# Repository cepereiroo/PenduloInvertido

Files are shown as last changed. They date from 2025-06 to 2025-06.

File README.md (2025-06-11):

# PenduloInvertido_Cecilia
En este repositorio se encuentra tanto la práctica 4 cómo la práctica 6 de la asignatura de Teoría de Control.

Además en la carpeta DiseñoPendulo se encuentra el esquemático eléctrico, el diseño de la PCB y el modelo 3D STL del chasis para su impresión.

**PRÁCTICA 4 - PID en tiempo discreto** 

Esta práctica tiene como objetivo implementar una biblioteca de controladores PID en tiempo discreto para ser utilizada en un microcontrolador ESP32, con aplicación directa en el control de un péndulo invertido. Esta biblioteca será utilizada en el desarrollo del proyecto de control descrito en el capítulo 6 del guión de prácticas. 

Se desarrollarán tres variantes del controlador PID en tiempo discreto: 

- **PID** : utiliza aproximaciones hacia atrás para las derivadas y sumas acumulativas para la integral. 
- **PID como filtro IIR**: modelado mediante transformada Z, facilitando su implementación como filtro digital. 
- **PID filtro baja** : se le pone un filtro al término derivativo para evitar que el ruido o los cambios bruscos del error afecten al control. 

Cada implementación está basada en los pseudocódigos del guión.  

Esta práctica está encapsulada en la carpeta libraries donde nos encontraremos :  

**I2Cdev/** 

Contiene archivos fuente y cabeceras que permiten la comunicación mediante el protocolo I2C. Es una biblioteca comúnmente usada para facilitar la lectura y escritura con sensores como el MPU6050 

**MPU6050/** 

Incluye las definiciones y funciones específicas para el sensor MPU6050, que proporciona mediciones de aceleración y giroscopio. Esta biblioteca se apoya en I2Cdev para obtener los datos del sensor y es esencial para calcular la posición y velocidad angular del péndulo. 

**PIDController/** 

Es la biblioteca desarrollada para está práctica para implementar los tres tipos de controladores PID discretos: 

- PID directo 
- PID como filtro IIR 
- PID filtro pasa baja

Dentro de cada carpeta estarán los archivos .h y .cpp con la implementación de las clases PID 

Se añadirá además una carpeta examples que contendrá tres ejemplos simples que muestran cómo usar cada una de las variantes del controlador PID implementadas. 

**CodigoCompletoPendulo.ino** 

Este es el sketch código principal de Arduino que integra las bibliotecas anteriores. Aquí se encuentra el código de control que: 

- Lee el ángulo del péndulo usando el MPU6050 
- Calcula la señal de control con el PID 
- Aplica la corrección al actuador 
- Permite probar y comparar las distintas variantes del controlador PID 

**PRÁCTICA 6 - Péndulo Invertido** 

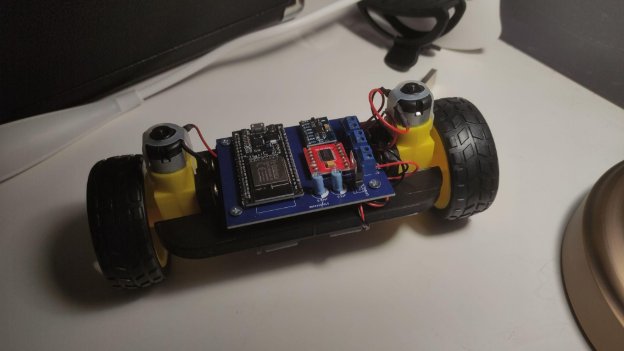
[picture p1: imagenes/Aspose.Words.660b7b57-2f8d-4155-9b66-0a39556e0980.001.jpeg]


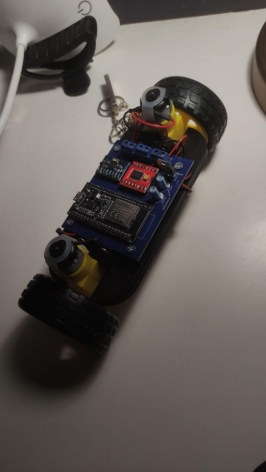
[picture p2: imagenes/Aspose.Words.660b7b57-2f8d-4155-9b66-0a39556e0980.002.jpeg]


En esta memoria se documenta el desarrollo de un prototipo funcional de un sistema de control para un péndulo invertido sobre ruedas, utilizando una ESP32 como unidad de control. El objetivo principal es mantener el equilibrio del péndulo en posición vertical mediante un controlador PID. 

Metodología seguida 

**Revisión de trabajos previos** 

Se investigaron diferentes proyectos relacionados con el péndulo invertido. 

**Definición de objetivos** 

Los objetivos del sistema se centraron en la estabilidad, la capacidad de recuperación tras perturbaciones y la interacción con el usuario mediante mando Bluetooth. 

**Selección del hardware** 

Se eligieron componentes accesibles y económicos que permitan un montaje sencillo y una buena integración con el entorno de desarrollo en C++. 

**Diseño del sistema físico** 

El chasis se diseñó buscando una estructura equilibrada, estable y lo más ligera posible, para facilitar la respuesta del sistema. 

**Programación y pruebas de control PID** 

Se implementó un controlador PID discreto en la ESP32, aplicando distintas versiones del algoritmo (con y sin filtro derivativo) y ajustando sus constantes. 
# **6.1 Hardware**   
**ESP32** 

Como unidad central de procesamiento utilicé una placa ESP32, concretamente un modelo disponible en Amazon por unos 11€. Este microcontrolador se conecta al ordenador mediante USB y permite cargar el código desde el entorno de Arduino.  

**MPU-6050** 

El sensor MPU-6050 fue el elegido para medir la orientación del robot, ya que incorpora un acelerómetro y un giroscopio en un solo módulo. Esta información es clave para mantener el equilibrio, especialmente con un margen inferior a 5 grados de inclinación.  

**Condensadores** 

En el circuito se añadieron dos condensadores: uno de 0,1 µF y otro de 0,22 µF. Estos se usaron para estabilizar la señal y reducir el ruido en ciertas conexiones críticas del sistema. 

**Bloques terminales** 

Para facilitar la conexión entre la batería y los motores, se instalaron bloques terminales. Esto permite una conexión firme y organizada del cableado. Se usaron tres en total, uno para cada motor y otro para la alimentación principal. 

**TB6612FNG** 

Para el control de los motores se optó por el TB6612FNG, un driver más eficiente y moderno que el clásico puente H. Con un precio inferior a los 2€, permite controlar dos motores de forma simultánea e independiente.  

**Batería** 

Alimenté el sistema con un portapilas de 4 pilas AA, conectado directamente a los bornes de alimentación de la placa. 

**Motores y ruedas** 

Se emplearon motores DC con reductora, muy comunes en robótica educativa. Vienen acompañados de ruedas compatibles que se acoplan directamente al eje del motor, facilitando el montaje. 

**Regulador de voltaje** 

Para asegurar un suministro eléctrico estable, se incorporó un regulador LM7805. Este componente mantiene la tensión en 5V, protegiendo así los elementos sensibles del circuito.  

# 6.2 PCB 
Se diseñó una placa PCB que permitiera  integrar todos los componentes del sistema de forma ordenada y funcional. El objetivo principal fue lograr un diseño limpio y claro, con un enrutado de pistas sencillo que permita identificar fácilmente las conexiones entre pines, lo cual es fundamental a la hora de soldar los componentes con precisión y sin errores. 

También se prestó especial atención al tamaño de la placa, tratando de mantener unas dimensiones reducidas. Esto facilita el montaje dentro del chasis del robot y evita que el conjunto final sea demasiado voluminoso, lo que podría afectar al equilibrio o la estética del prototipo. 

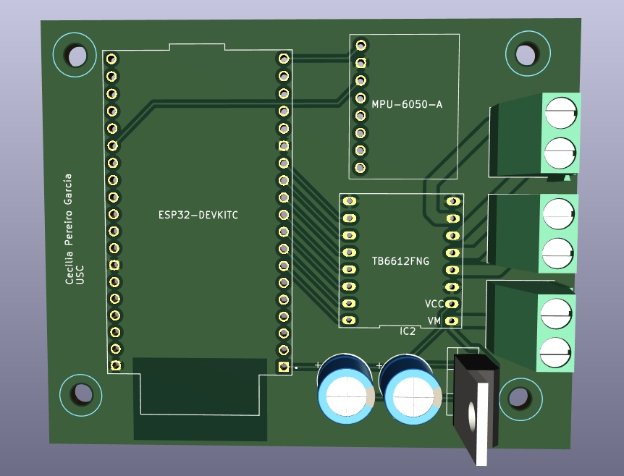
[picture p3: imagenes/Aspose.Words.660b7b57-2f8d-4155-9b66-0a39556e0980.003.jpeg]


**6.3 Diseño Chasis** 

Uno de los aspectos clave en el rendimiento del péndulo invertido es la ubicación del centro de gravedad. Es esencial que esté lo más próximo posible al suelo, ya que un centro de gravedad alto dificulta seriamente la estabilidad del sistema. Además, también es importante que el peso esté bien distribuido y centrado respecto al eje de las ruedas. Si el robot está equilibrado por diseño, se mantendrá en posición vertical incluso estando apagado, lo que facilita en gran medida el ajuste del controlador PID más adelante. 

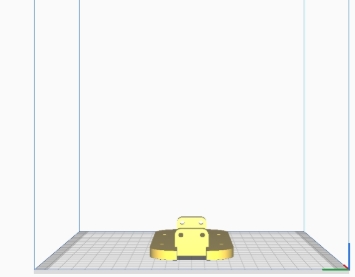
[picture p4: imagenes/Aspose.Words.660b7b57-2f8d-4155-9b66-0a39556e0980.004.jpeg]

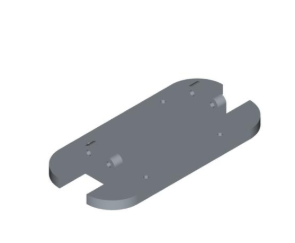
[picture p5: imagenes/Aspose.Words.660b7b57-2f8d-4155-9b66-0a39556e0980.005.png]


Este fue el diseño que hice en FreeCad donde monté el péndulo. 

Le añadí agujeros para poder fijar la PCB con tornillos y también unas elevaciones en los lados para sujetar los motores en vertical. Este diseño ya se adapta perfectamente a todo lo que necesitaba, así que fue el que usé para imprimir en 3D. 

El proceso de impresión a pesar de ser sencillo dió algún problema a la hora de imprimir por material atascado y otras complicaciones pero finalmente después de unas 5 horas se imprimió. 

**6.4 Diseño Chasis**

El proceso de montaje es bastante directo: simplemente hay que seguir el diseño de la PCB y conectar cada componente en su sitio. Los sensores se conectan tal como se planificó, sin necesidad de hacer cambios extra. 

Uno de los puntos clave es la alimentación eléctrica, ya que los motores y la ESP32 funcionan con voltajes diferentes. Para evitar problemas, es necesario usar un regulador de voltaje. En mi caso, los motores van con 9V, mientras que la ESP32 se alimenta con 5V, utilizando su pin de 5V directamente. 
# **6.5 Ajuste del PID** 
Para que el robot se mantenga en equilibrio, es necesario ajustar correctamente los valores del controlador PID. Cada una de sus tres partes tiene un efecto distinto sobre el comportamiento del sistema, así que es importante entender bien cómo funciona cada una. 

Orden sugerido para ajustar 

Primero se ajusta Kp: Este valor es el que permite que el robot empiece a reaccionar y trate de levantarse. Se sube poco a poco hasta que se vea que el robot intenta mantenerse en pie. Una vez encontrado un valor útil, se anota y se deja en 0 para pasar al siguiente paso. 

Después se trabaja con Kd: Esta parte se encarga de suavizar el movimiento y reducir las oscilaciones. Se busca un valor con el que el robot no se mueva bruscamente y casi logre mantenerse estable. 

Ahora se vuelve a poner Kp en el valor anotado anteriormente y se deja Kd como está. En esta fase, Ki aún sigue en 0, ya que solo se ajusta si el robot no termina de mantenerse en su sitio. 

Finalmente, se ajusta Ki: Esta constante ayuda a corregir pequeños errores residuales y que el robot alcance con más precisión la posición vertical. Pero si Kp y Kd no están bien ajustados, Ki no va a hacer milagros. 
# **Problemas**  
Durante la fase final del proyecto al intentar cargar el programa final en la ESP32 desde el entorno de Arduino empecé a tener varios problemas de conexión. Aunque conseguí que el ordenador la reconociera todo apuntaba a que el propio componente podría estar defectuoso. 

El error que aparecía de forma visible  era que el pin G0 debía estar en modo programación, así que pensé que podía tratarse de un fallo en el diseño de la PCB. Intenté forzar el estado del pin conectándolo a tierra mediante un puente, pero el mensaje de error seguía apareciendo. 

Tras comprobar con el multímetro que todos los valores eran correctos y que no había cortocircuitos evidentes, decidí aislar la ESP32 para comprobar si el fallo venía realmente de la placa o si el problema estaba en el circuito. 

Tenía dos opciones: cortar las pistas conectadas a la ESP32 (opción que me proporcionó el profesor Enrique) o desoldarla completamente. Al final opté por desoldarla, y aunque fue un proceso lento y delicado finalmente lo conseguí. Al probar la placa por separado verifiqué que estaba defectuosa. 

Elegí esta opción porque de esta forma lo único que tendría que cambiar a futuro sería el componente y no estropeo así la placa. 

Por falta de tiempo no he podido conseguir otra unidad así que el proyecto quedó interrumpido en esa etapa.

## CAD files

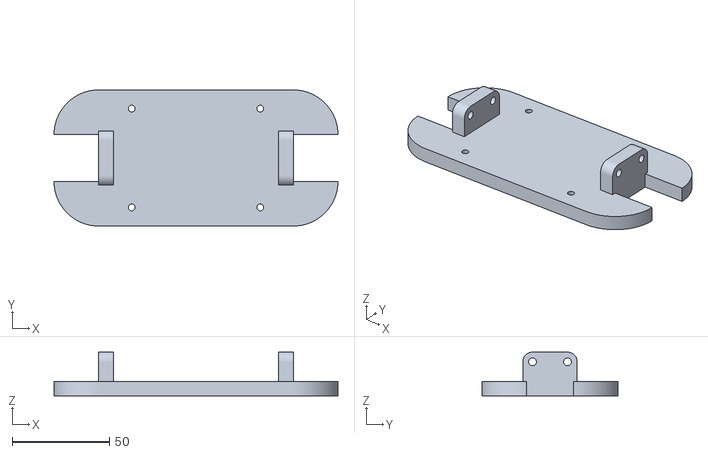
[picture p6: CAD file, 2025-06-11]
DiseñoPendulo/Pendulo_Inverso-Cuerpo.stl
146.0 x 70.0 x 22.5

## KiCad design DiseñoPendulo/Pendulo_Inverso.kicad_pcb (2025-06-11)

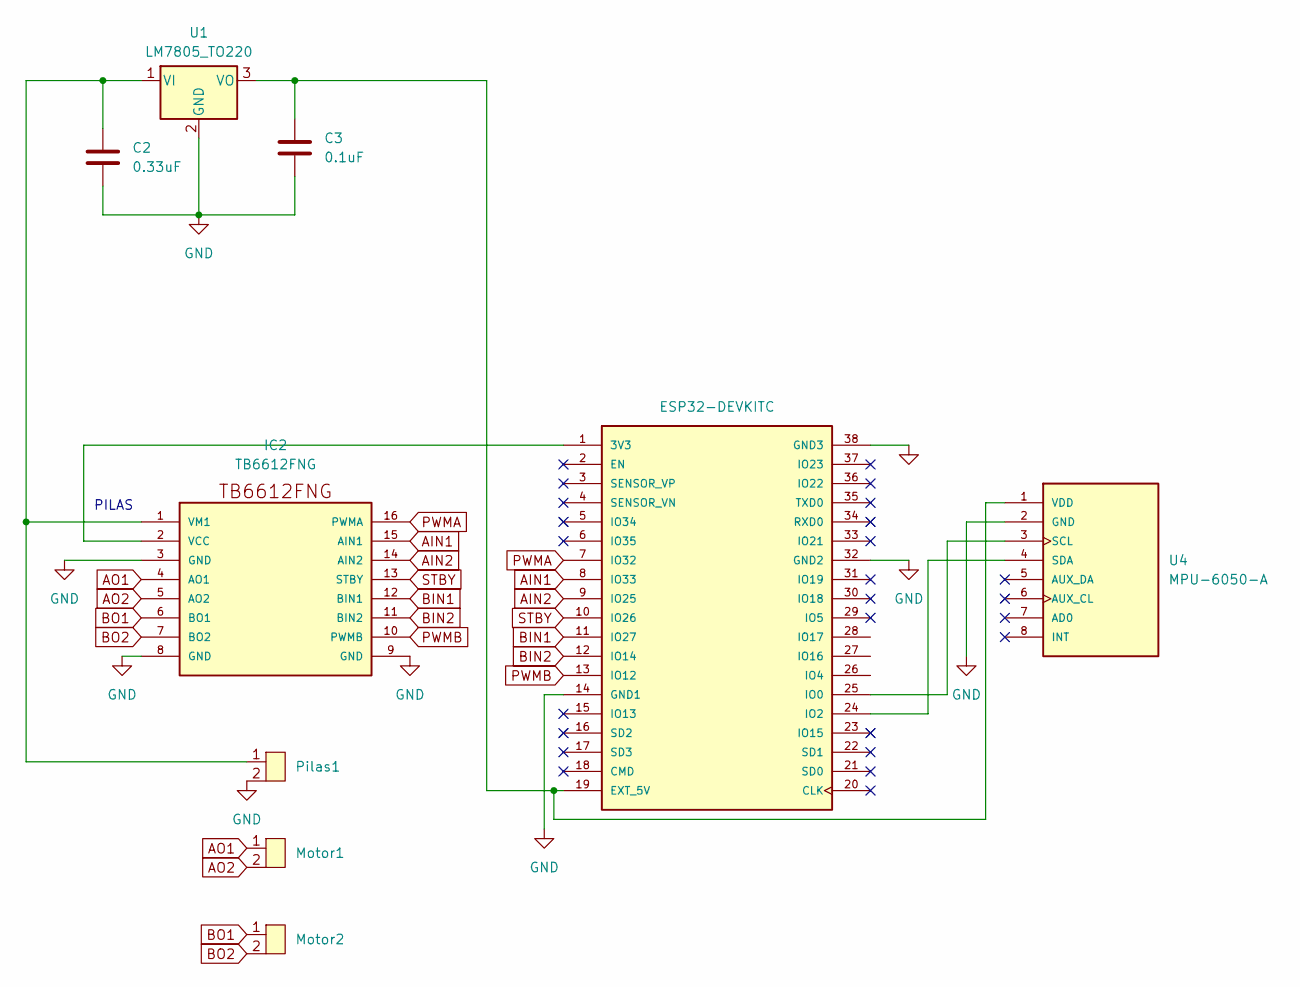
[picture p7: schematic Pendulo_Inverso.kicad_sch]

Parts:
C2: 0.33uF; CP_Radial_D8.0mm_P3.50mm
C3: 0.1uF; CP_Radial_D8.0mm_P3.50mm
IC2: TB6612FNG; TB6612FngSparkfun
Motor1, Motor2: TerminalBlock_Phoenix_MKDS-1,5-2_1x02_P5.00mm_Horizontal
Pilas1: TerminalBlock_Phoenix_MKDS-1,5-2_1x02_P5.00mm_Horizontal
U1: LM7805_TO220; TO-220-3_Vertical
U2: ESP32-DEVKITC; MODULE_ESP32-DEVKITC; PARTREV N/A
U4: MPU-6050-A; MPU6050; PARTREV 3.4

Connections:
AIN1: IC2.15 (AIN1), U2.8 (IO33)
AIN2: IC2.14 (AIN2), U2.9 (IO25)
AO1: IC2.4 (AO1), Motor1.1
AO2: IC2.5 (AO2), Motor1.2
BIN1: IC2.12 (BIN1), U2.11 (IO27)
BIN2: IC2.11 (BIN2), U2.12 (IO14)
BO1: IC2.6 (BO1), Motor2.1
BO2: IC2.7 (BO2), Motor2.2
GND: C2.2, C3.2, IC2.3 (GND), IC2.8 (GND), IC2.9 (GND), Pilas1.2, U1.2 (GND), U2.14 (GND1), U2.32 (GND2), U2.38 (GND3), U4.2 (GND)
unnamed: IC2.2 (VCC), U2.1 (3V3)
unnamed: C2.1, IC2.1 (VM1), Pilas1.1, U1.1 (VI)
unnamed: C3.1, U1.3 (VO), U2.19 (EXT_5V), U4.1 (VDD)
unnamed: U2.25 (IO0), U4.3 (SCL)
unnamed: U2.24 (IO2), U4.4 (SDA)
PWMA: IC2.16 (PWMA), U2.7 (IO32)
PWMB: IC2.10 (PWMB), U2.13 (IO12)
STBY: IC2.13 (STBY), U2.10 (IO26)

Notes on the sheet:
PILAS

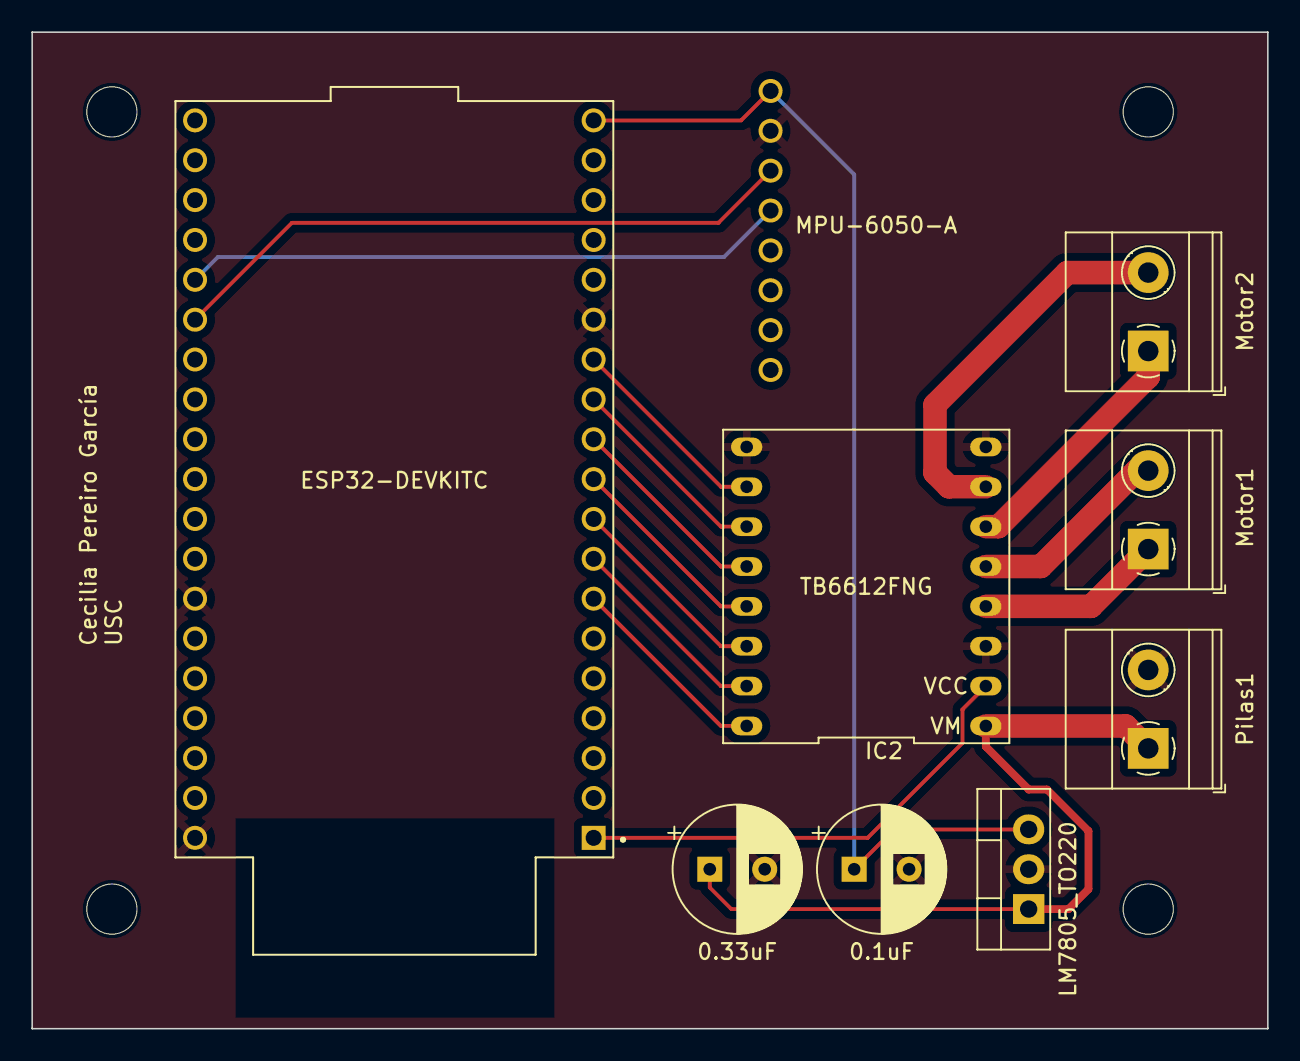
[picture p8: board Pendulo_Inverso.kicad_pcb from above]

Board: 2 copper layers, 78.7 x 63.5 mm, 9 parts (0 on the bottom side), 17 nets.
